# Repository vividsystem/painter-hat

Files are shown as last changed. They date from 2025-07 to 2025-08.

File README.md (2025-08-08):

# painter-hat
## A stepper motor hat that sucks less.
<div style="display: flex; flex-direction: row;">


</div>


Disclaimer: I haven't gotten the possibility to actually manufacture this yet. Therefore it might not work

Features:
* dual stepper-motor driver control <br>
* 100W USB-C PD to power motors and raspberry pi <br>
* support for A4988, TMC2208, TMC2209, etc. driver modules including UART control <br>
* meant as a replacement for [Waveshare Stepper Motor HAT](https://www.waveshare.com/wiki/Stepper_Motor_HAT)<sup>*</sup> <br><br><br>

<sup>*</sup>not completely hot-swap. you will have to use a different firmware

## Motivation 
I was very frustrated working with the [Waveshare Stepper Motor HAT](https://www.waveshare.com/wiki/Stepper_Motor_HAT).
The quality control seems to be off as two HATs I ordered didn't work. 
Their documentation is good and the provided codes works but there are some minor issues that led me to write my own code to
control the hat. Most importantly you can't swap drivers (in case you fry them for example) which led me to buy multiple
new drivers after testing and subsequently frying the drivers. This sucks because for my use case I have to get a whole
new HAT even when one of the two drivers is still working.

## Schematic
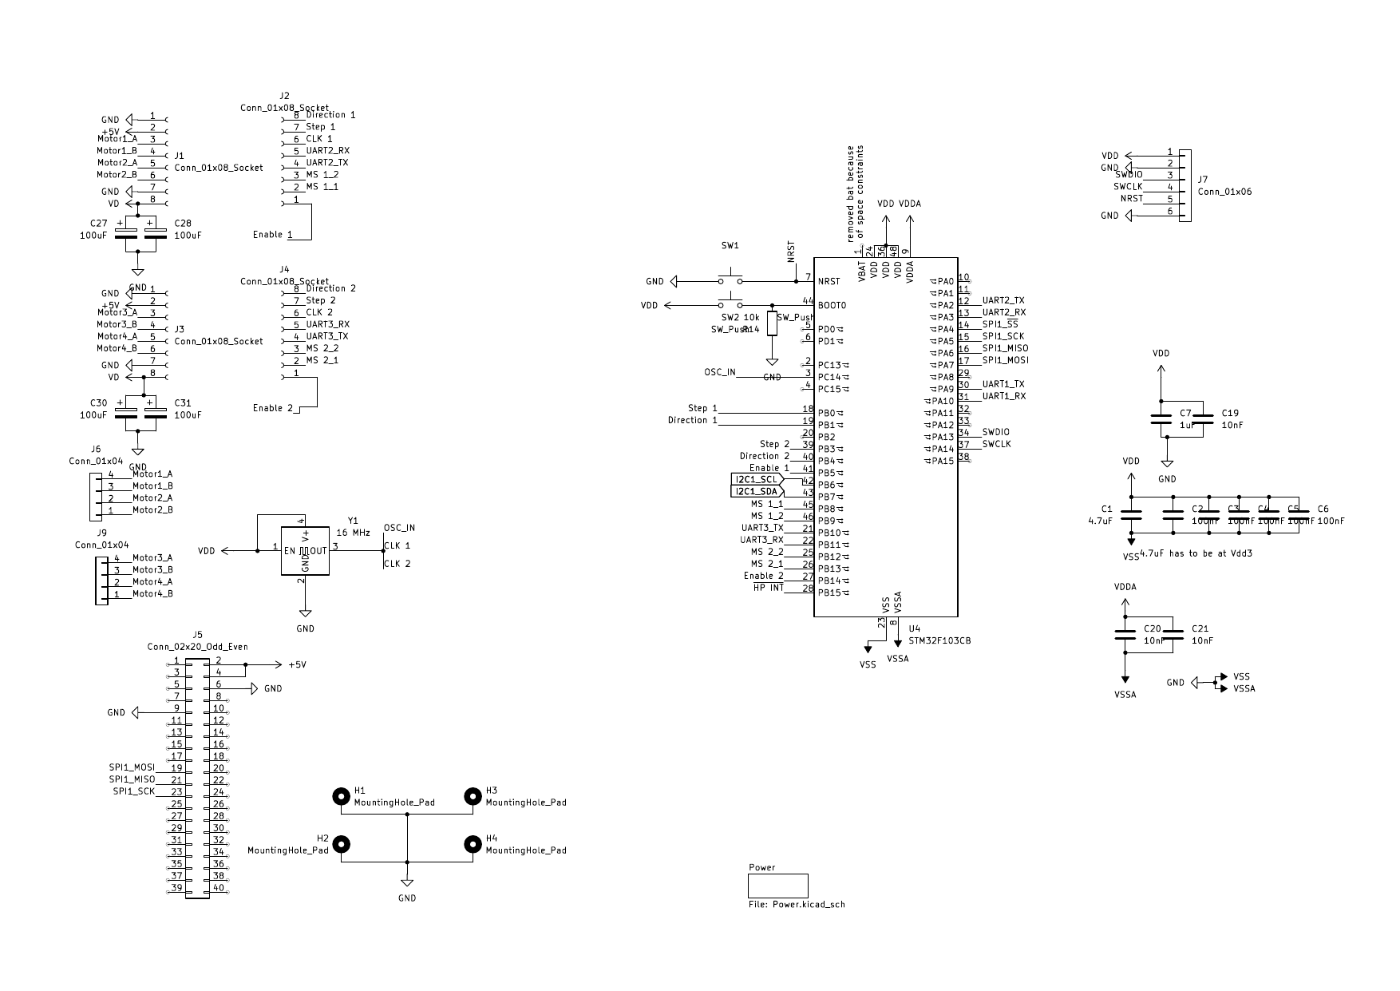
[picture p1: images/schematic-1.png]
Schematic Main

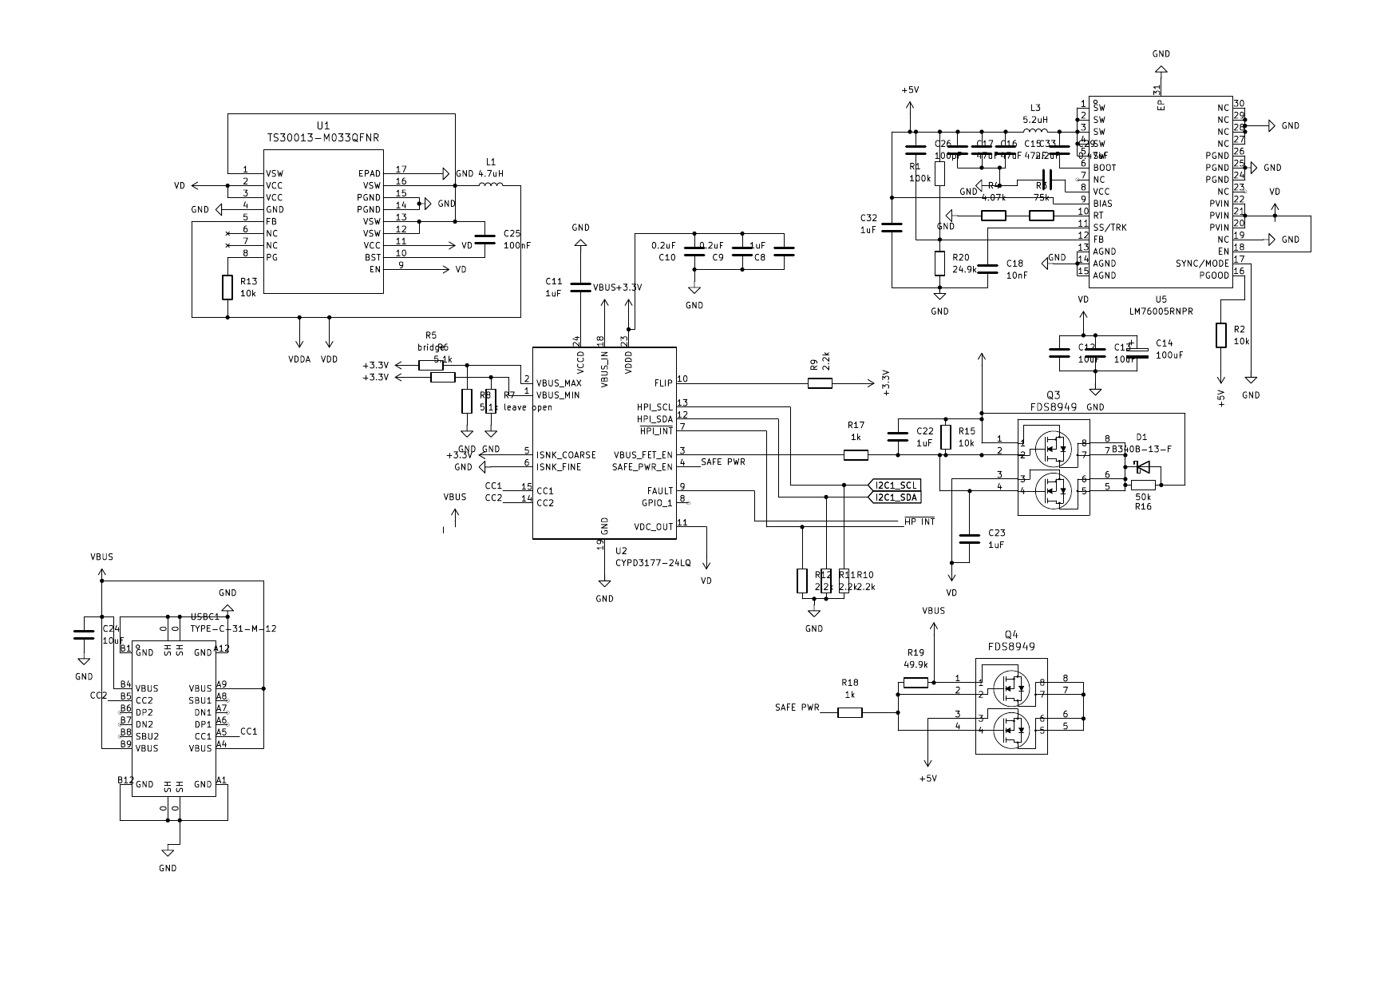
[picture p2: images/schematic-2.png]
Schematic Power


## PCB
### Top Layer - Signal
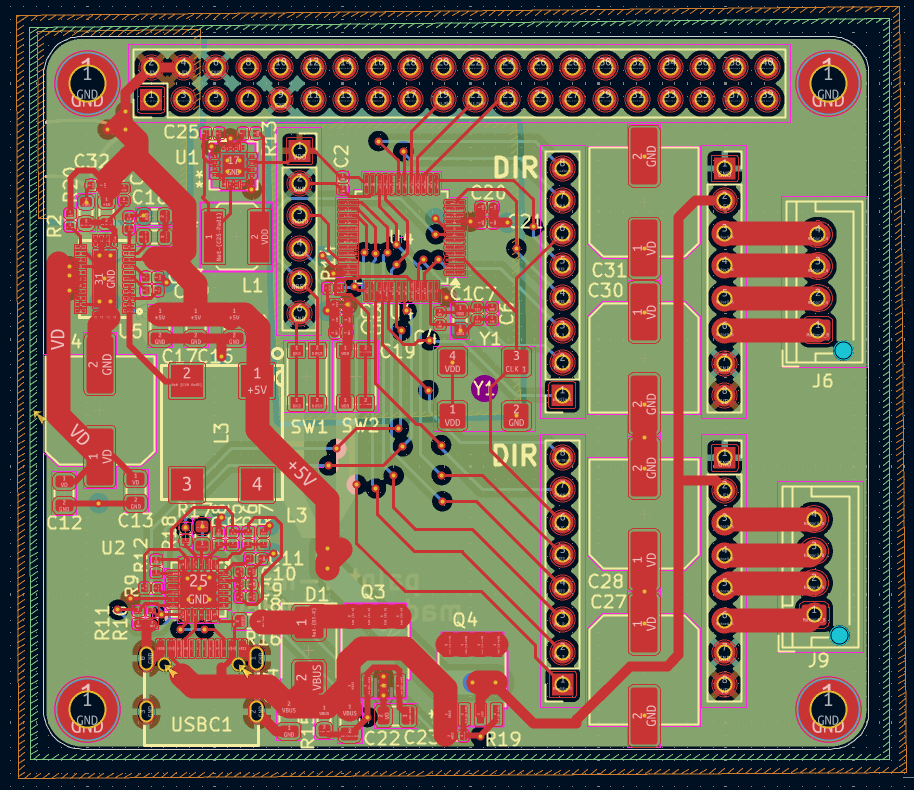
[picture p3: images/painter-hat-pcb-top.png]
PCB Top

### 1st Internal Layer - Ground 
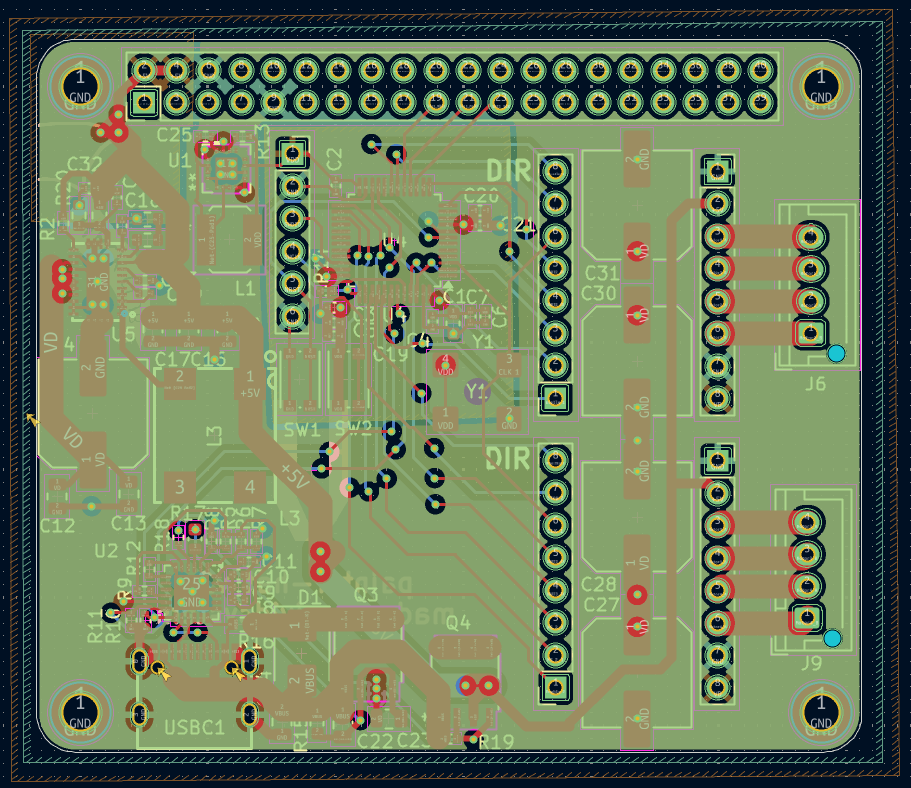
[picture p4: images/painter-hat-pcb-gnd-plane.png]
PCB GND

### 2nd Internal Layer - Power 
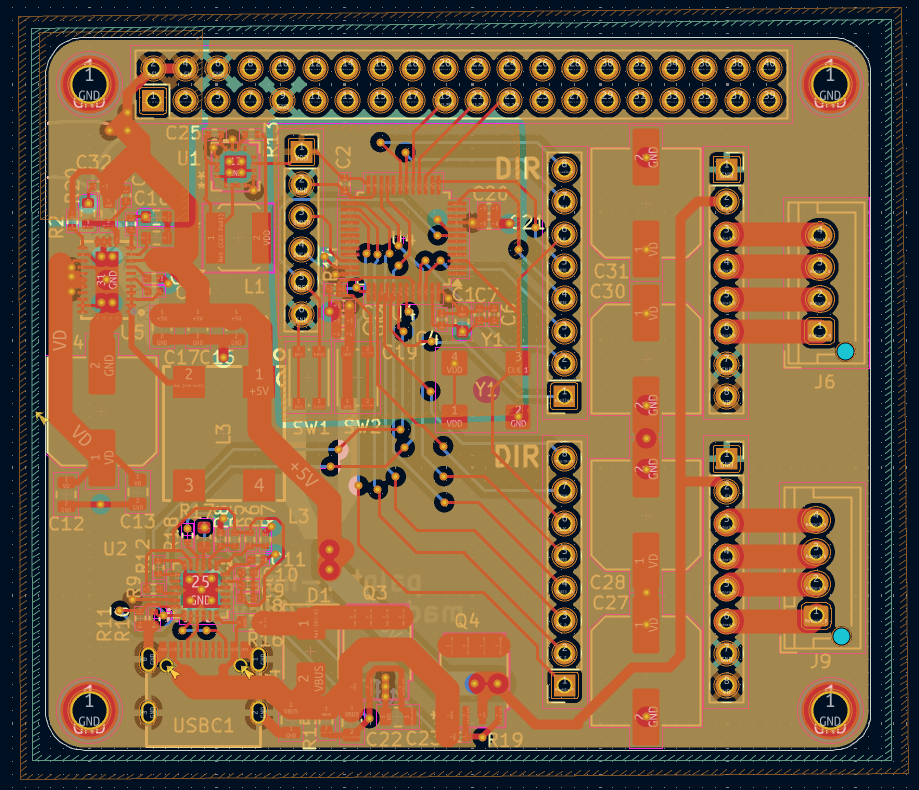
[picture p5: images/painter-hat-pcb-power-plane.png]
PCB Power

### Bottom Layer - Signal with GND Copper Fill 
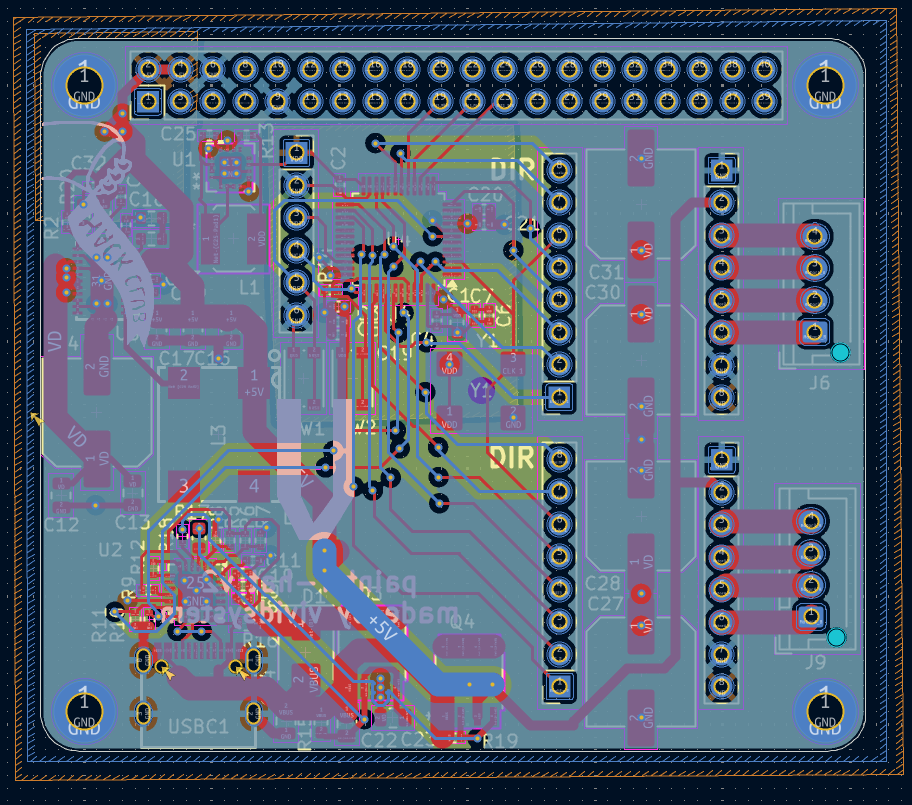
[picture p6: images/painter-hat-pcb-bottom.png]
PCB Bottom


## DIY it
It is about 155.58€ for the minimum PCBA PCB amount on JLCPCB.

## Firmware
Currently outdated!

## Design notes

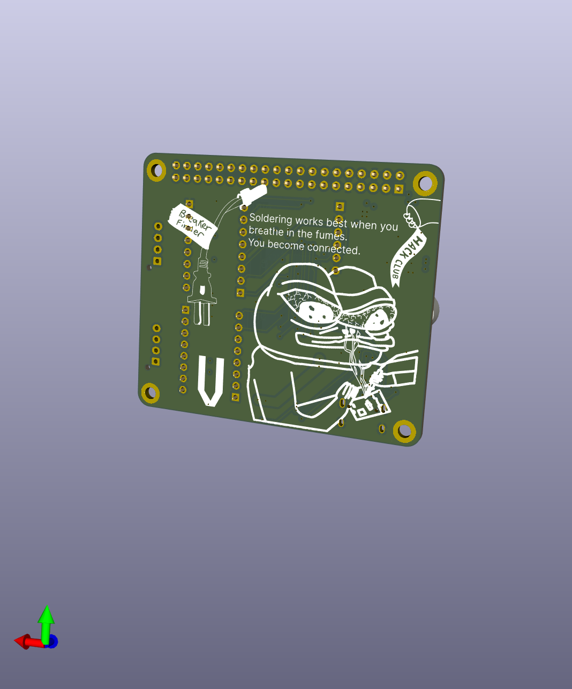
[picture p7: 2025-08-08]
images/painter-hat-back.png

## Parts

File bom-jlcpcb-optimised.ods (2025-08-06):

Top Designator | Comment | Footprint | Part # | Footprint | JLCPCB Part # | Lib Type | Qty | Total Price ($)
C1 | 4.7uF | 0603 | GRM188R6YA475KE15D | 0603 | C162274 | Extended | 9 | 0.3393
C2,C3,C4,C5,C6,C25 | 100nF | 0402 | CL05B104KB54PNC | 0402 | C307331 | Basic | 30 | 0.132
C10,C9 | 0.2uF | 0402 | CL05B224KO5NNNC | 0402 | C16772 | Basic | 10 | 0.042
C11,C32,C7,C8 | 1uF | 0402 | CL05A105KA5NQNC | 0402 | C52923 | Basic | 20 | 0.06
C12,C13,C24 | 10uF | 0805 | GRM21BR61H106KE43L | 0805 | C440198 | Basic | 15 | 0.981
C14,C27,C28,C30,C31 | 100uF | C_Elec_8x10.2 | UWT1H101MNL1GS | SMD,D8xL10mm | C445063 | Extended | 26 | 4.3368
C15,C16,C17 | 47uF | 0805 | GRM21BR61A476ME15L | 0805 | C124129 | Extended | 17 | 2.4412
C18,C19,C20,C21 | 10nF | 0402 | CL05B103KB5NNNC | 0402 | C15195 | Basic | 20 | 0.026
C22,C23 | 1uF | 0805 | CL21B105KBFNNNE | 0805 | C28323 | Basic | 10 | 0.089
C26 | 100pF | 0402 | 0402CG101J500NT | 0402 | C1546 | Basic | 5 | 0.005
C29 | 0.47uF | 0402 | CL05A474KA5NNNC | 0402 | C92361 | Extended | 20 | 0.222
C33 | 2.2uF | 0402 | CL05A225KO5NQNC | 0402 | C170151 | Extended | 20 | 0.118
D1 | B340B-13-F | D_SMB | SS34 | SMA(DO-214AC) | C8678 | Basic | 5 | 0.138
J1,J2,J3,J4 | Conn_01x08_Socket | PinSocket_1x08_P2.54mm_Vertical | 2.54-1*8P母环保 | 插件,P=2.54mm | C27438 | Extended | 20 | 1.5
J5 | Conn_02x20_Odd_Even | PinHeader_2x20_P2.54mm_Vertical | 2.54-2*20 | 插件,P=2.54mm | C2977589 | Extended | 5 | 1.056
J6,J9 | Conn_01x04 | JST_XH_B4B-XH-AM_1x04_P2.50mm_Vertical | B4B-XH-AM(LF)(SN) | 插件,P=2.5mm | C161871 | Extended | 11 | 0.8338
J7 | Conn_01x06 | PinSocket_1x06_P2.54mm_Vertical | 2.54-1*6P母 | 插件,P=2.54mm | C40877 | Extended | 5 | 0.342
L1 | 4.7uH | IND_NRS5030T100MMGJ_TAY | NRS5030T4R7MMGJV | SMD,4.9x4.9mm | C2880386 | Extended | 5 | 1.129
L3 | 5.2uH | IND-SMD_4P-L10.5-W9.5-TL | CDEPI99NP-5R0PC | SMD-4P,10.5x9.5mm | C171582 | Extended | 5 | 10.1625
Q3,Q4 | FDS8949 | SOIC8_3P9X4P9_OSI | FDS8949 | SO-8 | C10874 | Extended | 10 | 5.925
R1 | 100k | 0603 | TNPW0603100KBEEA | 0603 | C844888 | Extended | 7 | 0.6909
R3 | 75k | 0603 | 0603WAF7502T5E | 0603 | C23242 | Basic | 5 | 0.005
R4 | 4.07k | 0603 | ARG03FTC4001N | 0603 | C2984443 | Extended | 20 | 0.132
R5 | bridge | 0402 | HBRIDGEKIT2GOTOBO1 | - | C17636950 | Extended | 0 | 0
R6,R8 | 5.1k | 0402 | 0402WGF5101TCE | 0402 | C25905 | Basic | 10 | 0.005
R10,R11,R12,R9 | 2.2k | 0402 | 0402WGF2201TCE | 0402 | C25879 | Basic | 20 | 0.01
R13,R14,R2 | 10k | 0402 | 0402WGJ0103TCE | 0402 | C25531 | Extended | 27 | 0.0108
R15 | 10k | 0603 | 0603WAJ0103T5E | 0603 | C15401 | Extended | 20 | 0.016
R16 | 50k | 0603 | PNM0603E5002BST5 | 0603 | C2073717 | Extended | 5 | 12.0075
R17 | 1k | 0603 | ESR03EZPF1001 | 0603 | C2653986 | Extended | 20 | 0.24
R18 | 1k | 0402 | CRCW04021K00FKEDHP | 0402 | C313354 | Extended | 20 | 0.438
R19 | 49.9k | 0402 | 0402WGF4992TCE | 0402 | C25897 | Extended | 20 | 0.01
R20 | 24.9k | 0603 | FRC0603F2492TS | 0603 | C2930080 | Extended | 20 | 0.018
SW1,SW2 | SW_Push | SW_Push_1P1T_NO_CK_KMR2 | KMR421NGLFS | SMD-4P,4.2x2.8mm | C221687 | Extended | 10 | 5.43
U2 | CYPD3177-24LQ | QFN-24-1EP_4x4mm_P0.5mm_EP2.75x2.75mm | CYPD3177-24LQXQ | QFN-24 | C2959321 | Extended | 5 | 7.6425
U4 | STM32F103CB | LQFP-48_7x7mm_P0.5mm | STM32F103CBT6 | LQFP-48(7x7) | C8304 | Extended | 5 | 9.8175
U5 | LM76005RNPR | WQFN-30_L6.0-W4.0-P0.50-TL-EP_LM76005RNPR | LM76005RNPR | WQFN-30-EP(4x6) | C2866241 | Extended | 5 | 19.005
USBC1 | TYPE-C-31-M-12 | USB-C_SMD-TYPE-C-31-M-12 | TYPE-C-31-M-12 | SMD | C165948 | Extended | 5 | 0.8485
Y1 | 16MHz | Oscillator_SMD_EuroQuartz_XO91-4Pin_7.0x5.0mm | X322516MLB4SI | SMD3225-4P | C13738 | Basic | 5 | 0.321
U1 | TS30013-M033QFNR | QFN16_3X3_SEM | TS30013-M033QFNR | VQFN-16-EP(3x3) | C2071049 | Extended | 5 | 0
R7 | leaveopen | 0402 | No Part Selected

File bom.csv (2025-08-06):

Designator | Footprint | Quantity | Value | LCSC Part #
SW1, SW2 | SW_Push_1P1T_NO_CK_KMR2 | 2 | SW_Push | C221679
C1 | 0603 | 1 | 4.7uF | C162274
C10, C9 | 0402 | 2 | 0.2uF | C2180912
C11, C32, C7, C8 | 0402 | 4 | 1uF | C5596482
C12, C13, C24 | 0805 | 3 | 10uF | C2932476
C14, C27, C28, C30, C31 | C_Elec_8x10.2 | 5 | 100uF | C445063
C15, C16, C17 | 0805 | 3 | 47uF | C124129
C18, C19, C20, C21 | 0402 | 4 | 10nF | C15195
C2, C3, C4, C5, C6, C25 | 0402 | 5 | 100nF | C22333701
C22, C23 | 0805 | 2 | 1uF | C28323
C26 | 0402 | 1 | 100pF | C281751
C29 | 0402 | 1 | 0.47uF | C92361
C33 | 0402 | 1 | 2.2uF | C170151
D1 | D_SMB | 1 | B340B-13-F | C154551
J1, J2, J3, J4 | PinSocket_1x08_P2.54mm_Vertical | 4 | Conn_01x08_Socket | C27438
J5 | PinHeader_2x20_P2.54mm_Vertical | 1 | Conn_02x20_Odd_Even | C2977589
J6, J9 | JST_XH_B4B-XH-AM_1x04_P2.50mm_Vertical | 2 | Conn_01x04 | C161871
J7 | PinSocket_1x06_P2.54mm_Vertical | 1 | Conn_01x06 | C40877
L1 | IND_NRS5030T100MMGJ_TAY | 1 | 4.7uH | C2880386
L3 | IND-SMD_4P-L10.5-W9.5-TL | 1 | 5.2uH | C171582
Q3, Q4 | SOIC8_3P9X4P9_OSI | 2 | FDS8949 | C10874
R1 | 0603 | 1 | 100k | C844888
R10, R11, R12, R9 | 0402 | 4 | 2.2k | C82680
R13, R14, R2 | 0402 | 3 | 10k | C7501196
R15 | 0603 | 1 | 10k | C327830
R16 | 0603 | 1 | 50k | C2073717
R17 | 0603 | 1 | 1k | C2653986
R18 | 0402 | 1 | 1k | C4162025
R19 | 0402 | 1 | 49.9k | C4043528
R20 | 0603 | 1 | 24.9k | C2930080
R3 | 0603 | 1 | 75k | C42783
R4 | 0603 | 1 | 4.07k | C861435
R5 | 0402 | 1 | bridge
R6, R8 | 0402 | 2 | 5.1k | C6221081
R7 | 0402 | 1 | leave open
U1 | QFN16_3X3_SEM | 1 | TS30013-M033QFNR | C2071049
U2 | QFN-24-1EP_4x4mm_P0.5mm_EP2.75x2.75mm | 1 | CYPD3177-24LQ | C2959321
U4 | LQFP-48_7x7mm_P0.5mm | 1 | STM32F103CB | C8304
U5 | WQFN-30_L6.0-W4.0-P0.50-TL-EP_LM76005RNPR | 1 | LM76005RNPR | C2866241
USBC1 | USB-C_SMD-TYPE-C-31-M-12 | 1 | TYPE-C-31-M-12 | C165948
Y1 | Oscillator_SMD_EuroQuartz_XO91-4Pin_7.0x5.0mm | 1 | 16 MHz | C596923

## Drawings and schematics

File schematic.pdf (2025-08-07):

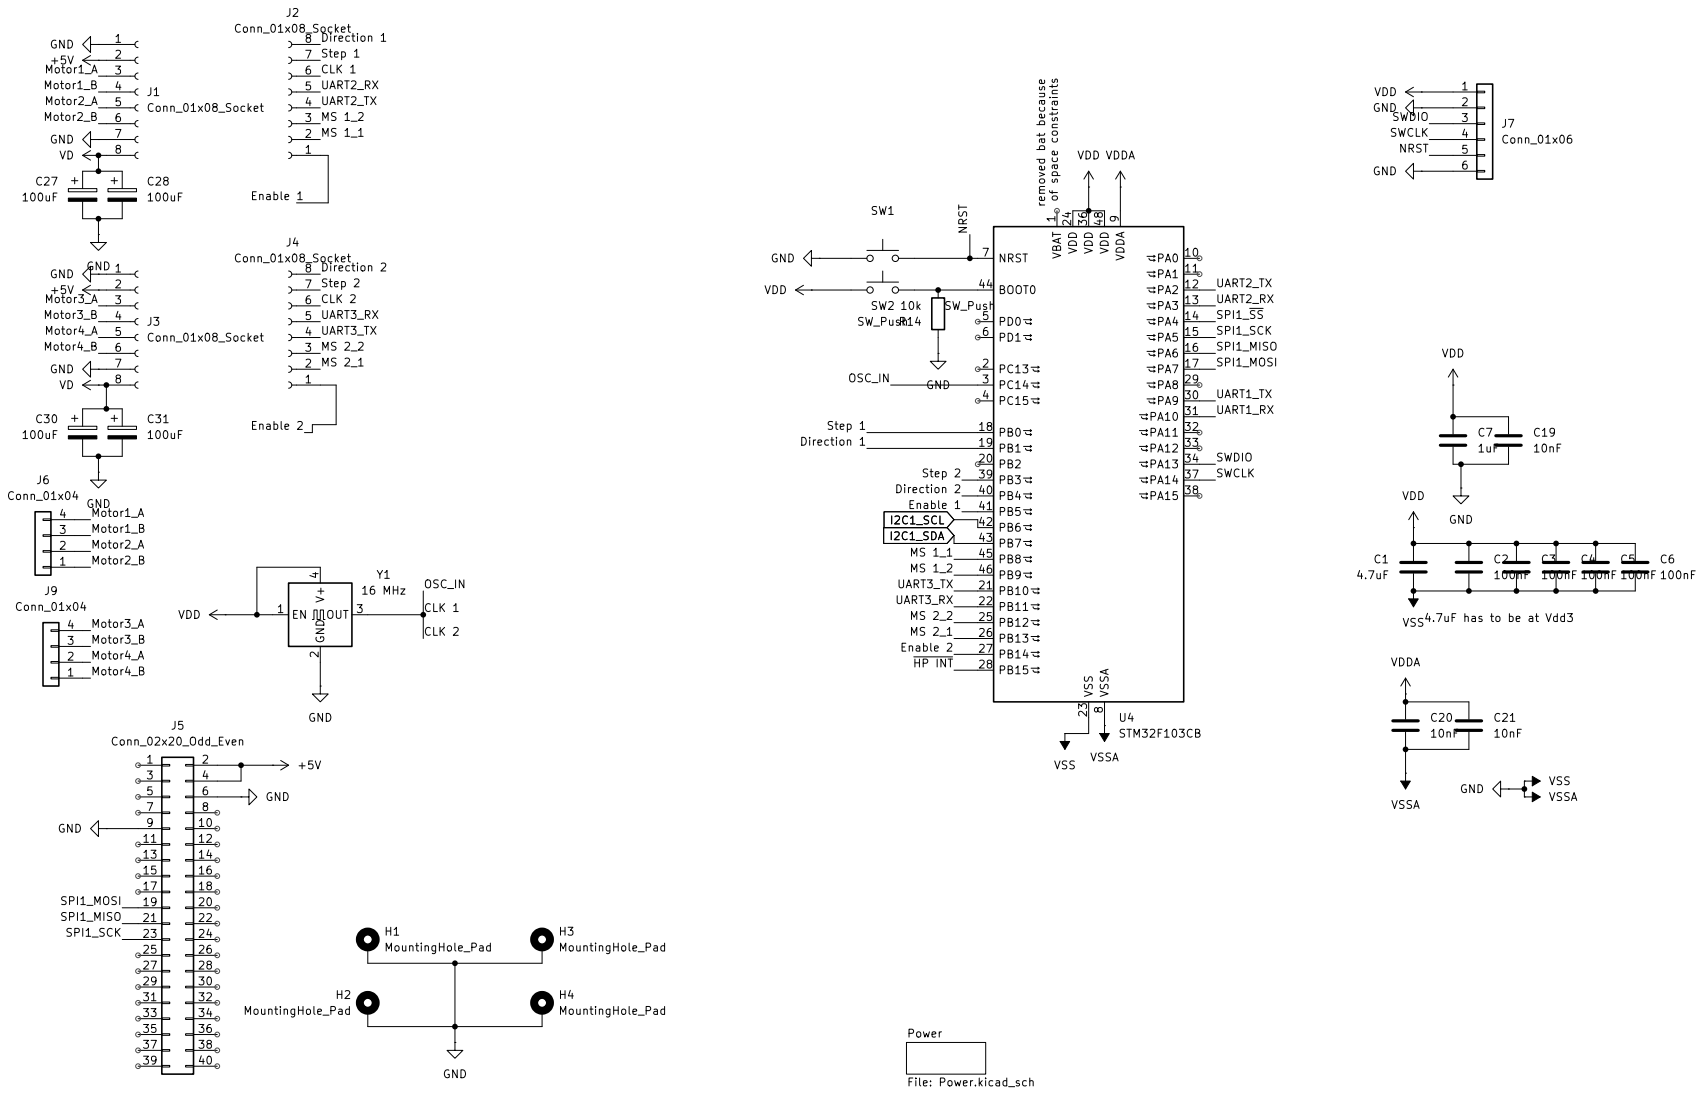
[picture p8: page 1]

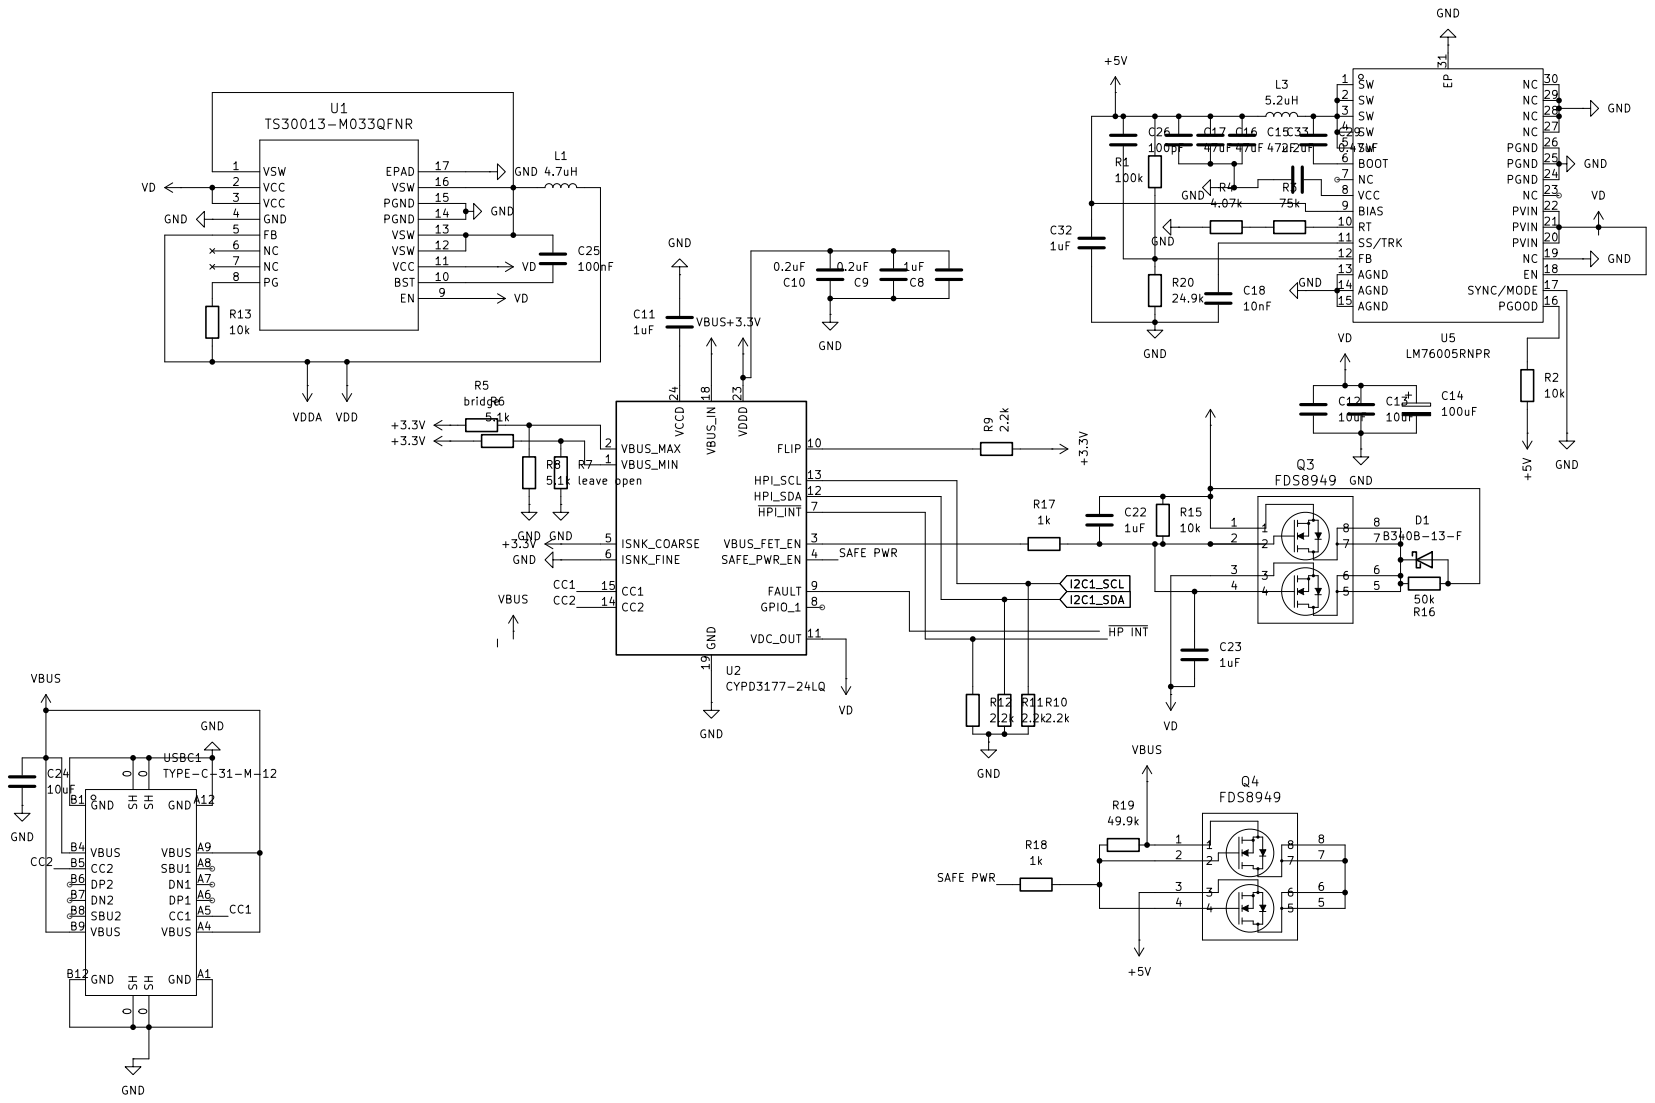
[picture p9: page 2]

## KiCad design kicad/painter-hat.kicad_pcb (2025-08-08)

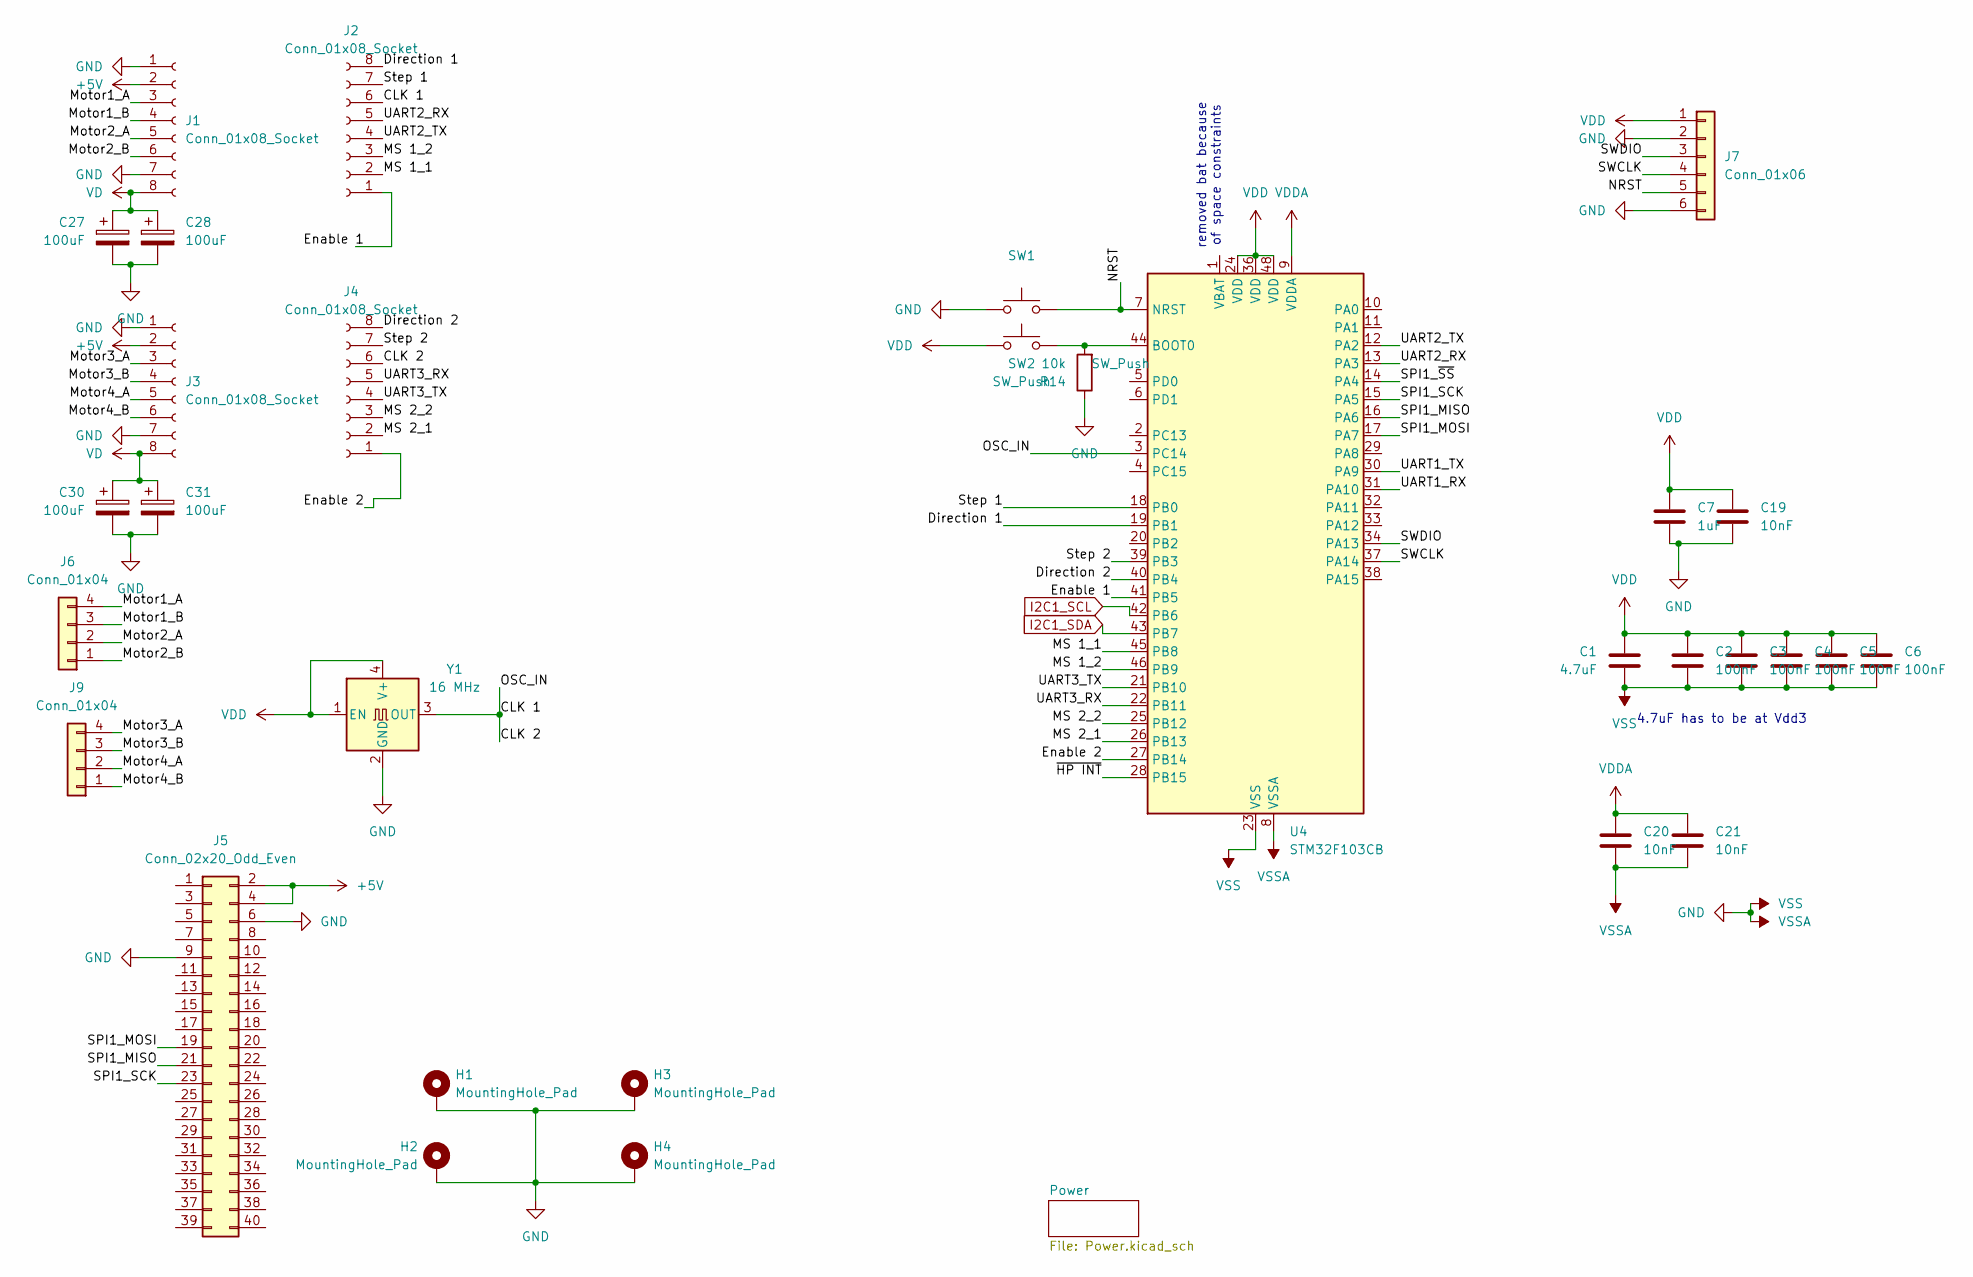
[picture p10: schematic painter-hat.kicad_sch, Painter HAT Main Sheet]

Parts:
C1: 4.7uF; C_0603_1608Metric
C2, C3, C4, C5, C6: 100nF; C_0402_1005Metric
C7: 1uF; C_0402_1005Metric
C19, C20, C21: 10nF; C_0402_1005Metric
C27, C28, C30, C31: 100uF; C_Elec_8x10.2
H1, H2, H3, H4: MountingHole_Pad; MountingHole_2.7mm_M2.5_DIN965_Pad_TopBottom
J1, J2, J3, J4: Conn_01x08_Socket; PinSocket_1x08_P2.54mm_Vertical
J5: Conn_02x20_Odd_Even; PinHeader_2x20_P2.54mm_Vertical
J6, J9: Conn_01x04; JST_XH_B4B-XH-AM_1x04_P2.50mm_Vertical
J7: Conn_01x06; PinSocket_1x06_P2.54mm_Vertical
R14: 10k; R_0402_1005Metric
SW1, SW2: SW_Push; SW_Push_1P1T_NO_CK_KMR2
U4: STM32F103CB; LQFP-48_7x7mm_P0.5mm
Y1: 16 MHz; Oscillator_SMD_EuroQuartz_XO91-4Pin_7.0x5.0mm

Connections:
+5V: J1.2, J3.2, J5.2, J5.4; also elsewhere on the board
/CLK 1: J2.6, J4.6, U4.3 (PC14), Y1.3 (OUT)
/Direction 1: J2.8, U4.19 (PB1)
/Direction 2: J4.8, U4.40 (PB4)
/Enable 1: J2.1, U4.41 (PB5)
/Enable 2: J4.1, U4.27 (PB14)
/MS 1_1: J2.2, U4.45 (PB8)
/MS 1_2: J2.3, U4.46 (PB9)
/MS 2_1: J4.2, U4.26 (PB13)
/MS 2_2: J4.3, U4.25 (PB12)
/Motor1_A: J1.3, J6.4
/Motor1_B: J1.4, J6.3
/Motor2_A: J1.5, J6.2
/Motor2_B: J1.6, J6.1
/Motor3_A: J3.3, J9.4
/Motor3_B: J3.4, J9.3
/Motor4_A: J3.5, J9.2
/Motor4_B: J3.6, J9.1
/NRST: J7.5, SW1.2, U4.7 (NRST)
/SPI1_MISO: J5.21, U4.16 (PA6)
/SPI1_MOSI: J5.19, U4.17 (PA7)
/SPI1_SCK: J5.23, U4.15 (PA5)
/SPI1_~SS: U4.14 (PA4)
/SWCLK: J7.4, U4.37 (PA14)
/SWDIO: J7.3, U4.34 (PA13)
/Step 1: J2.7, U4.18 (PB0)
/Step 2: J4.7, U4.39 (PB3)
/UART1_RX: U4.31 (PA10)
/UART1_TX: U4.30 (PA9)
/UART2_RX: J2.5, U4.13 (PA3)
/UART2_TX: J2.4, U4.12 (PA2)
/UART3_RX: J4.5, U4.22 (PB11)
/UART3_TX: J4.4, U4.21 (PB10)
/~HP INT: U4.28 (PB15)
GND: C1.2, C2.2, C3.2, C4.2, C5.2, C6.2, C7.2, C19.2, C20.2, C21.2, C27.2, C28.2, C30.2, C31.2, H1.1, H2.1, H3.1, H4.1, J1.1, J1.7, J3.1, J3.7, J5.6, J5.9, J7.2, J7.6, R14.1, SW1.1, U4.8 (VSSA), U4.23 (VSS), U4.35 (VSS), U4.47 (VSS), Y1.2 (GND); also elsewhere on the board
I2C1_SCL: U4.42 (PB6); also elsewhere on the board
I2C1_SDA: U4.43 (PB7); also elsewhere on the board
unnamed: R14.2, SW2.2, U4.44 (BOOT0)
VD: C27.1, C28.1, C30.1, C31.1, J1.8, J3.8; also elsewhere on the board
VDD: C1.1, C2.1, C3.1, C4.1, C5.1, C6.1, C7.1, C19.1, C20.1, C21.1, J7.1, SW2.1, U4.9 (VDDA), U4.24 (VDD), U4.36 (VDD), U4.48 (VDD), Y1.1 (EN), Y1.4 (V+); also elsewhere on the board

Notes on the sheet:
4.7uF has to be at Vdd3
removed bat because of space constraints

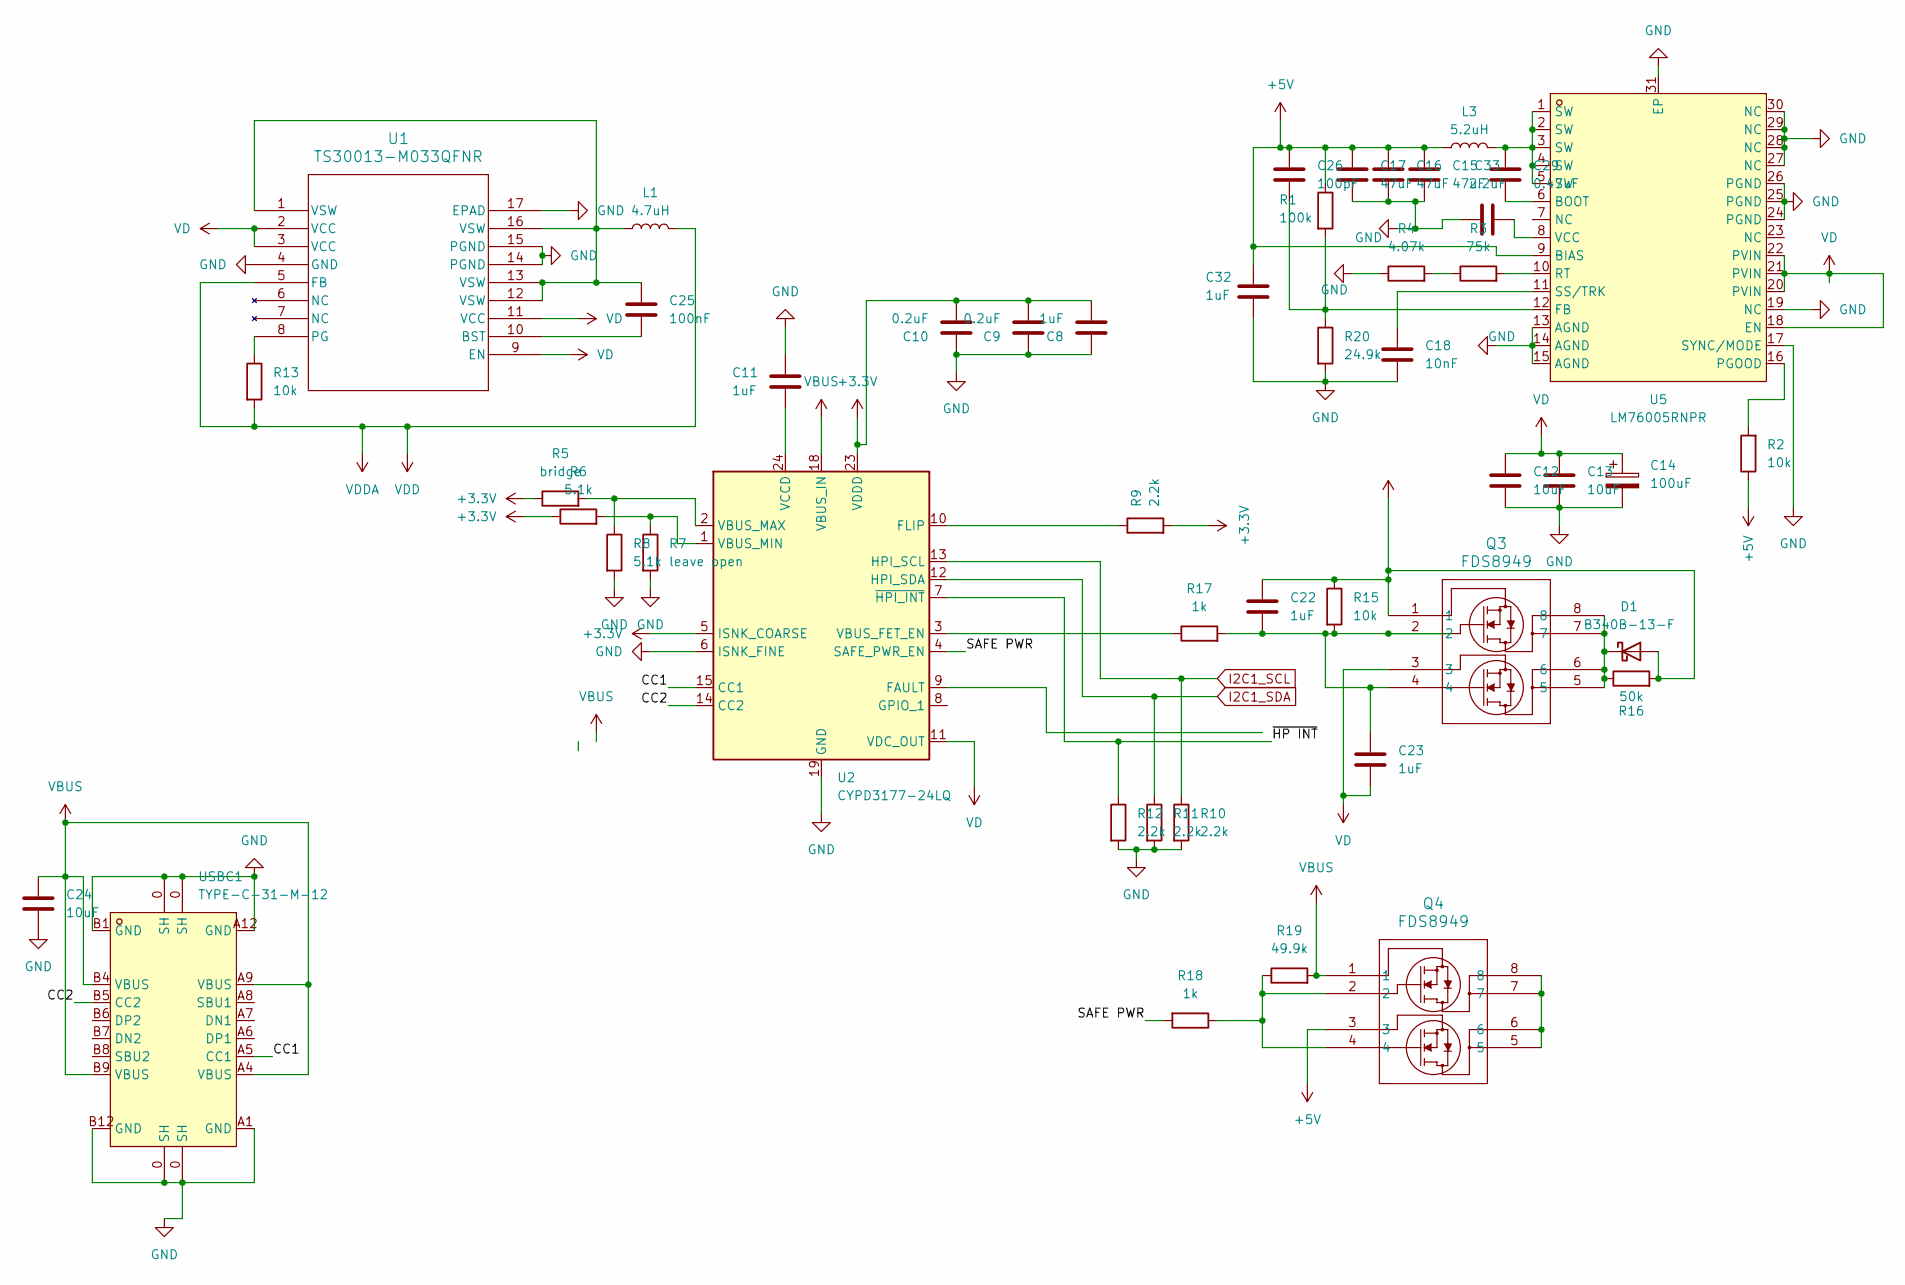
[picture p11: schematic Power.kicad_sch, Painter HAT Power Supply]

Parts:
C8, C11, C32: 1uF; C_0402_1005Metric
C9, C10: 0.2uF; C_0402_1005Metric
C12, C13, C24: 10uF; C_0805_2012Metric
C14: 100uF; C_Elec_8x10.2
C15, C16, C17: 47uF; C_0805_2012Metric
C18: 10nF; C_0402_1005Metric
C22, C23: 1uF; C_0805_2012Metric
C25: 100nF; R_0402_1005Metric
C26: 100pF; C_0402_1005Metric
C29: 0.47uF; C_0402_1005Metric
C33: 2.2uF; C_0402_1005Metric
D1: B340B-13-F; D_SMB
L1: 4.7uH; IND_NRS5030T100MMGJ_TAY
L3: 5.2uH; IND-SMD_4P-L10.5-W9.5-TL
Q3, Q4: FDS8949; SOIC8_3P9X4P9_OSI
R1: 100k; R_0603_1608Metric
R2, R13: 10k; R_0402_1005Metric
R3: 75k; R_0603_1608Metric
R4: 4.07k; R_0603_1608Metric
R5: bridge; R_0402_1005Metric
R6, R8: 5.1k; R_0402_1005Metric
R7: leave open; R_0402_1005Metric
R9, R10, R11, R12: 2.2k; R_0402_1005Metric
R15: 10k; C_0603_1608Metric
R16: 50k; R_0603_1608Metric
R17: 1k; C_0603_1608Metric
R18: 1k; R_0402_1005Metric
R19: 49.9k; R_0402_1005Metric
R20: 24.9k; R_0603_1608Metric
U1: TS30013-M033QFNR; QFN16_3X3_SEM
U2: CYPD3177-24LQ; QFN-24-1EP_4x4mm_P0.5mm_EP2.75x2.75mm
U5: LM76005RNPR; WQFN-30_L6.0-W4.0-P0.50-TL-EP_LM76005RNPR; LCSC Part C2866241
USBC1: TYPE-C-31-M-12; USB-C_SMD-TYPE-C-31-M-12; LCSC Part C165948

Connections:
+3.3V: C8.1, C9.2, C10.2, R5.1, R6.1, R9.2, U2.5 (ISNK_COARSE), U2.23 (VDDD)
+5V: C15.1, C16.1, C17.1, C26.1, C32.2, L3.1, Q4.3, R1.1, R2.1, U5.9 (BIAS); also elsewhere on the board
/Power/CC1: U2.15 (CC1), USBC1.A5 (CC1)
/Power/CC2: U2.14 (CC2), USBC1.B5 (CC2)
/Power/SAFE PWR: R18.2, U2.4 (SAFE_PWR_EN)
/Power/~HP INT: R12.1, U2.7 (~HPI_INT)
GND: C8.2, C9.1, C10.1, C11.1, C12.2, C13.2, C14.2, C15.2, C16.2, C17.2, C18.2, C24.1, C32.1, C33.1, R4.1, R7.2, R8.2, R10.2, R11.2, R12.2, R20.2, U1.4 (GND), U1.14 (PGND), U1.15 (PGND), U1.17 (EPAD), U2.6 (ISNK_FINE), U2.19 (GND), U2.22 (GND), U2.25 (GND), U5.13 (AGND), U5.14 (AGND), U5.15 (AGND), U5.17 (SYNC/MODE), U5.19 (NC), U5.24 (PGND), U5.25 (PGND), U5.26 (PGND), U5.27 (NC), U5.28 (NC), U5.29 (NC), U5.30 (NC), U5.31 (EP), USBC1.0 (SH), USBC1.1, USBC1.2, USBC1.3, USBC1.A1 (GND), USBC1.A12 (GND), USBC1.B1 (GND), USBC1.B12 (GND); also elsewhere on the board
I2C1_SCL: R10.1, U2.13 (HPI_SCL); also elsewhere on the board
I2C1_SDA: R11.1, U2.12 (HPI_SDA); also elsewhere on the board
unnamed: C22.2, C23.1, Q3.2, Q3.4, R15.2, R17.2
unnamed: C25.1, L1.1, U1.1 (VSW), U1.12 (VSW), U1.13 (VSW), U1.16 (VSW)
unnamed: C29.2, L3.2, U5.1 (SW), U5.2 (SW), U5.3 (SW), U5.4 (SW), U5.5 (SW)
unnamed: D1.1 (K), Q3.5, Q3.6, Q3.7, Q3.8, R16.1
unnamed: Q4.2, Q4.4, R18.1, R19.1
unnamed: Q4.5, Q4.6, Q4.7, Q4.8
unnamed: R3.1, R4.2
unnamed: C25.2, U1.10 (BST)
unnamed: R13.1, U1.8 (PG)
unnamed: R9.1, U2.10 (FLIP)
unnamed: R17.1, U2.3 (VBUS_FET_EN)
unnamed: R5.2, R8.1, U2.2 (VBUS_MAX)
unnamed: R6.2, R7.1, U2.1 (VBUS_MIN)
unnamed: C11.2, U2.24 (VCCD)
unnamed: C29.1, U5.6 (BOOT)
unnamed: C26.2, R1.2, R20.1, U5.12 (FB)
unnamed: R2.2, U5.16 (PGOOD)
unnamed: R3.2, U5.10 (RT)
unnamed: C18.1, U5.11 (SS/TRK)
unnamed: C33.2, U5.8 (VCC)
VBUS: C22.1, C24.2, D1.2 (A), Q3.1, Q4.1, R15.1, R16.2, R19.2, U2.18 (VBUS_IN), USBC1.A4 (VBUS), USBC1.A9 (VBUS), USBC1.B4 (VBUS), USBC1.B9 (VBUS)
VD: C12.1, C13.1, C14.1, C23.2, Q3.3, U1.2 (VCC), U1.3 (VCC), U1.9 (EN), U1.11 (VCC), U2.11 (VDC_OUT), U5.18 (EN), U5.20 (PVIN), U5.21 (PVIN), U5.22 (PVIN); also elsewhere on the board
VDD: L1.2, R13.2, U1.5 (FB); also elsewhere on the board

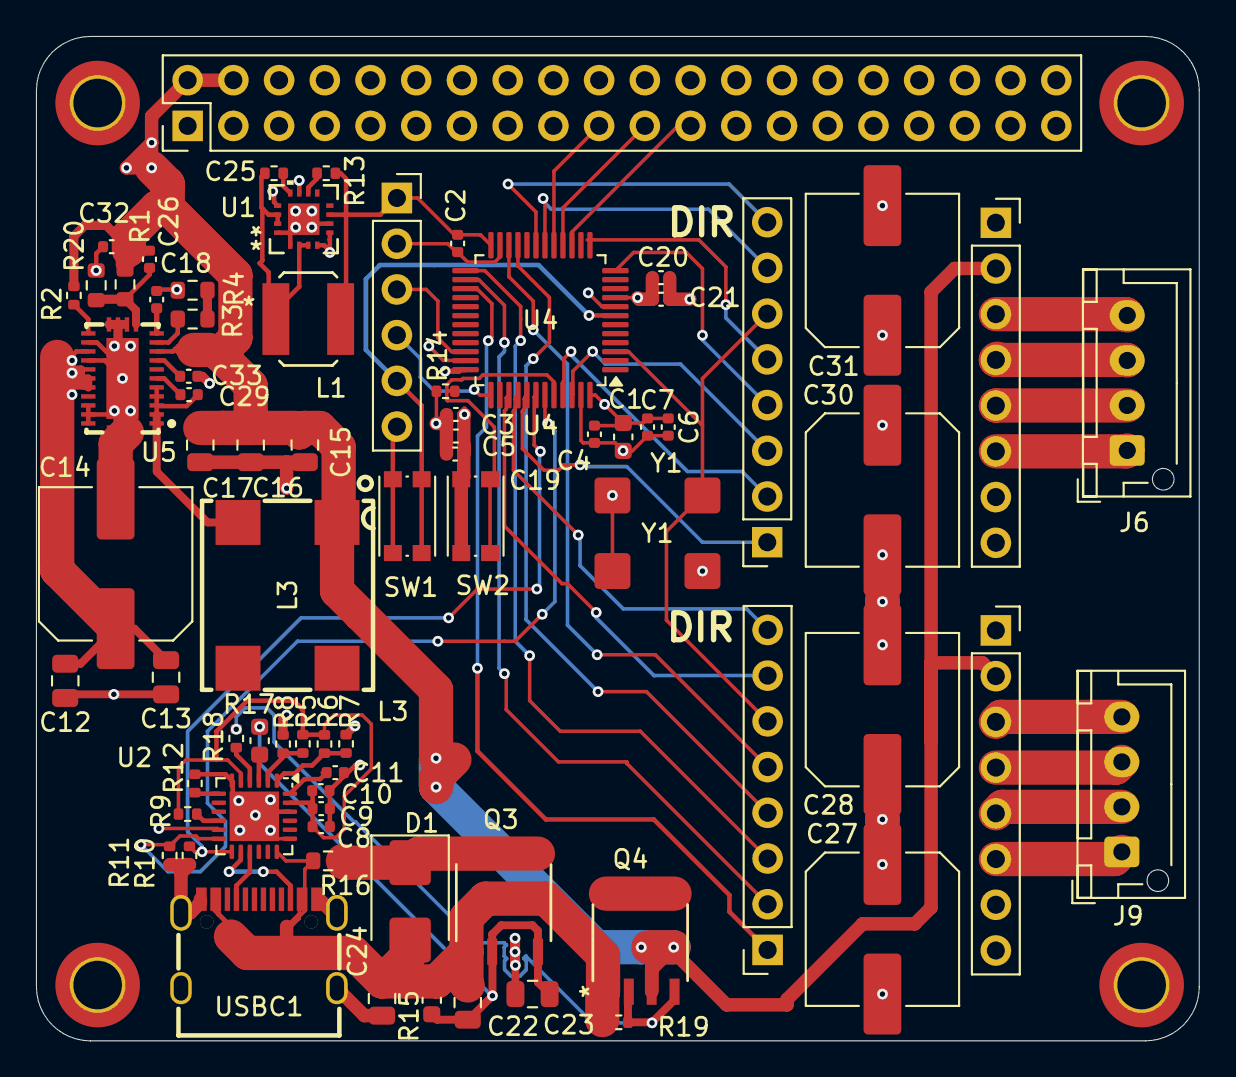
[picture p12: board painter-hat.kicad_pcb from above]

Board: 4 copper layers, 64.6 x 55.8 mm, 78 parts (0 on the bottom side), 62 nets.

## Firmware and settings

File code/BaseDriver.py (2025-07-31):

import RPi.GPIO as GPIO
import time

class BaseDriver():
    def __init__(self, dir_pin, step_pin, enable_pin, mode_pins):
        self.dir_pin = dir_pin
        self.step_pin = step_pin        
        self.enable_pin = enable_pin
        self.mode_pins = mode_pins
        
        GPIO.setmode(GPIO.BCM)
        GPIO.setwarnings(False)
        GPIO.setup(self.dir_pin, GPIO.OUT)
        GPIO.setup(self.step_pin, GPIO.OUT)
        GPIO.setup(self.enable_pin, GPIO.OUT)
        GPIO.setup(self.mode_pins, GPIO.OUT)
        
    def Stop(self):
        GPIO.output(self.enable_pin, 0)
    

        
    def TurnStep(self, steps, forward = True, stepdelay=0.005):
            
        GPIO.output(self.enable_pin, 1)
        GPIO.output(self.dir_pin, 0 if forward else 1)
        if (steps == 0):
            return
            
        for i in range(steps):
            GPIO.output(self.step_pin, True)
            time.sleep(stepdelay)
            GPIO.output(self.step_pin, False)
            time.sleep(stepdelay)

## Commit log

2025-07-31 feat(hw): basic wiring done
    [Power.kicad_sch, painter-hat.kicad_sch]
2025-07-31 finalized pcb
    [Power.kicad_sch, painter-hat.kicad_pcb, painter-hat.kicad_sch]
2025-08-05 feat: added bom
    [bom.csv]
2025-08-05 feat: v2
    [Power.kicad_sch, painter-hat.kicad_pcb, painter-hat.kicad_sch]
2025-08-05 fix: minor additions to v2
    [Power.kicad_sch, painter-hat.kicad_sch]
2025-08-06 docs: bom with lcsc part numbers
    [bom-lcsc.csv]
2025-08-06 feat: v2.1
    [Power.kicad_sch, bom-lcsc.csv, bom.csv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]
2025-08-06 feat: updated everything
    [Power.kicad_sch, bom.csv, painter-hat.kicad_pcb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]
2025-08-06 fix: updated pcb picture
2025-08-06 feat: pcb screens
2025-08-06 feat: added jlcpcb bom
    [bom-jlcpcb-optimised.ods]
2025-08-07 feat(v2.1.1): BOOT0, NRST Wiring, Polarized Caps fixed
    [Power.kicad_sch, painter-hat.kicad_pcb, painter-hat.kicad_sch]
2025-08-07 feat: added schematic images these were previously not added due to the misconfigured .gitignore
2025-08-08 feat: added community designs
    [painter-hat.kicad_pcb]
